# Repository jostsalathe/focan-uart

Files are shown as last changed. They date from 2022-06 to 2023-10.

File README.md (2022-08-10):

# focan-uart

Reverse engineering effort for the UART protocol used between Focan E-Scooter/-Bike displays (GZ3 is the actual test subject) and motor controllers.

## physical interface

The pinout of the connectors can be acquired from the *DU*s [user manual](./doc/2022-06-29%20Focan%20GZ-3%20user%20manual.pdf) and here are some additional details I deduced with the help of a multimeter and an oscilloscope:

| Pin # | Wire color | Function | Driven by | note |
| --- | --- | --- | --- | --- |
| 1 | red | battery voltage | *MCU* | *DU* draws about 11 mA when *MCU* is disconnected and 40 mA during normal operation (without lights). |
| 2 | blue | controller power | *DU* | This supplies power to the *MCU* including lights. *MCU* without lights draws about 29 mA during normal operation. |
| 3 | black | ground | *common* | Swapping this wire with #2 kills the *DU*. Ask me how I know. |
| 4 | green | UART RX | *MCU* to 0~3.32 V |  |
| 5 | yellow | UART TX | *DU* to 0~3.48 V | *MCU* connects 5k6 pullup from 5 V when `controller power` is supplied by *DU* |

## protocol analysis

The protocol analysis and documentation can be found in [./protocolAnalysis/README.md](./protocolAnalysis/README.md).

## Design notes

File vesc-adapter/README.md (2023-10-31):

# Adapter board for using the original Focan GZ3 Display for controlling a VESC6 motor controller

This project uses the UART interface of the VESC6 to translate the commands from the display unit to control and config commands for the VESC6 and extract motor status data from it to report sensible data back to the display unit.

The adapter also has to incorporate power distribution to the vehicle lighting as well as evaluation circuitry and logic for the break lever switches to cut power when breaks are applied (maybe even gradually apply regen?).

## shutting down the ESC

The display unit has a return path for the battery voltage which it switches on when it is turned on. This can be loaded with a few hundred mA. It originally enabled the motor controller and supplied the lights. But motor current would not run through this detour path.

The VESC6 has no enable input so we need a power switch to shut it off when the enable signal from the display unit is off. I started work on implementing a high side switch with a P channel MOSFET (turns out, one wouldn't be enough to dissipate the RDSon losses, two to four would be better).

I then realized by sheer luck through this [blog post](https://civilpedia.org/p/?t=Adding-Shutdown-to-VESC-6&pid=381) that the voltage supply on the VESC6 utilizes the buck converter that is integrated into the DRV8301 MOSFET driver IC to feed all the logic voltages. That IC has an enable pin for that buck converter that is unconnected (pulled high through internal pullup) on the VESC6 board.

When I pull that pin low, the whole VESC6 board only draws 0.74 mA @ 30 V. And the adapter board will also be supplied by this buck converter, so would draw nothing when disabled.

The approach in the aforementioned blog post should be suitable to our application as well. I have some 3V Zener diodes in stock. I measured the pullup current out of the Buck_En pin to be about 1.1 uA so 150k resistors should be plenty small to reliably pull the pin low whilst not wasting energy.

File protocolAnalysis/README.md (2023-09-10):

# High Level Analyzer for Saleae Logic 2

The protocol is analyzed by capturing the communication with a logic analyzer and looking for patterns. Any gained knowledge is then put into high level analyzer plugins (*HLA*) for that logic analyzer. This enables ongoing verification of previous insights.

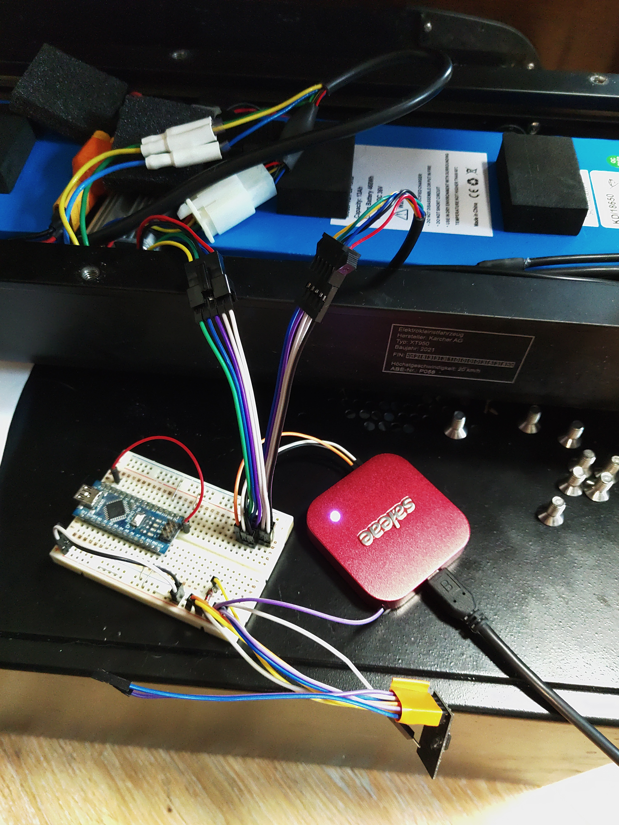
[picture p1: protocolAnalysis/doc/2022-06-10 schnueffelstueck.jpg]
Schnueffelstueck


There is one HLA each for the UART signal between the display unit (*DU*) and the motor control unit (*MCU*):

* `FocanGZ3-TX`: *DU* -> *MCU*
* `FocanGZ3-RX`: *MCU* -> *DU*

## General protocol description

The communication works with full duplex UART at about 3.5 V logic level running at 9600 baud.

As long as the *DU* is turned on, it will send a data frame to the *MCU* via the TX signal roughly every 0.1 seconds. The *MCU* will then reply to that via the RX signal.

## TX data frame

Each TX data frame consists of 20 bytes describing the whole configuration and state of the *DU*.

| **offset** | **mask** | **name** | **description** |
| --- | --- | --- | --- |
| 0x00 | 0xFF | device address (?) | seems to be always 1 in TX direction |
| 0x01 | 0xFF | data frame length | always 20  (0x14) in TX direction |
| 0x02 | 0xFF | protocol revision (?) | seems to be always 1 in both directions |
| *0x03* | *0xFC* | *unknown* |  |
| 0x03 | 0x03 | drive mode | 0: pedal drive, 1: electric drive, 2: both (set with P10) |
| *0x04* | *0xF0* | *unknown* |  |
| 0x04 | 0x0C | gear | 0: off, 1: eco, 2: mid, 3: high |
| 0x04 | 0x03 | gear again | repeated for some reason ¯\\\_(ツ)\_/¯ |
| *0x05* | *0x80* | *unknown* |  |
| 0x05 | 0x40 | kick start | 0: motor can start from still stand, 1: motor must turn before it can start (set with P09) |
| 0x05 | 0x20 | light enable | 0: light off, 1: light on |
| *0x05* | *0x1F* | *unknown* |  |
| 0x06 | 0xFF | number of speed magnets | ranging from 0 to 255 (set with P07) |
| *0x07* | *0xFE* | *unknown* |  |
| 0x07 | 0x01 | wheel diameter high | high byte of the following |
| 0x08 | 0xFF | wheel diameter low | in 1/10 inch ranging from 25 to 500 (set with P06) |
| *0x09* | *0xE0* | *unknown* |  |
| 0x09 | 0x1F | boost sensitivity | ranging from 1 to 24 (set with P11) |
| *0x0A* | *0xF8* | *unknown* |  |
| 0x0A | 0x07 | boost start strength | ranging from 0 to 5 (set with P12) |
| *0x0B* | *0xFF* | *unknown* |  |
| *0x0C* | *0x80* | *unknown* |  |
| 0x0C | 0x7F | speed limit | in km/h ranging from 0 to 100 (set with P08) |
| *0x0D* | *0xE0* | *unknown* |  |
| 0x0D | 0x1F | current limit | in A ranging from 1 to 20 (set with P14) |
| *0x0E* | *0xFC* | *unknown* | (maybe belonging to the following) |
| 0x0E | 0x03 | undervolt threshold high | high byte of the following |
| 0x0F | 0xFF | undervolt threshold low | in 1/10 volt (combination of P03 (range: 24V/36V/48V) and P15 (decivolt adjustment) |
| *0x10* | *0xFC* | *unknown* |  |
| 0x10 | 0x03 | speed lever position high | high byte of the following |
| 0x11 | 0xFF | speed lever position low | ranging from 0 to 1000 |
| *0x12* | *0x80* | *unknown* |  |
| 0x12 | 0x40 | cruise enable | (set with P17) |
| *0x12* | *0x30* | *unknown* |  |
| 0x12 | 0x0F | power magnetic steel disc type | 5/8/12 (set with P13) |
| 0x13 | 0xFF | CRC | check sum |

The CRC sum is calculated with the following algorithm parameters determined by the program [reveng](https://reveng.sourceforge.io/readme.htm) using captured samples:

`width=8  poly=0x01  init=0x00  refin=false  refout=false  xorout=0x00  check=0x31  residue=0x00  name=(none)`

## RX data frame

Each RX data frame consists of 14 bytes describing the state of the *MCU*.

| offset | mask | name | description |
| --- | --- | --- | --- |
| 0x00 | 0xFF | device address (?) | seems to be always 2 in RX direction |
| 0x01 | 0xFF | data frame length | always 14 (0x0E) in RX direction |
| 0x02 | 0xFF | protocol revision (?) | seems to be always 1 in both directions |
| *0x03* | *0xFF* | *unknown* |  |
| *0x04* | *0xFF* | *unknown* |  |
| *0x05* | *0xFF* | *unknown* |  |
| *0x06* | *0xFF* | *unknown* |  |
| *0x07* | *0xFF* | *unknown* |  |
| *0x08* | *0x80* | *unknown* |  |
| 0x08 | 0x7F | wheel speed high | high byte of the following |
| 0x09 | 0xFF | wheel speed low | in milliseconds/revolution ranging from 0 to 31456 |
| *0x0A* | *0xFF* | *unknown* |  |
| *0x0B* | *0xFF* | *unknown* |  |
| *0x0C* | *0xFF* | *unknown* |  |
| 0x0D | 0xFF | CRC | check sum |

The vehicle velocity `v[km/h]` can be calculated from the wheel speed `t[ms]` using the known wheel diameter `D[in]` like this:

```
circumference C[m] = 0.0254 m/in * D * PI

v = 1000 ms/s * 3600 s/h * 0.001 km/m * C / t
v = 3600 * C / t
v = 3600 * 0.0254 * D * PI / t
v = 91.44 * PI * D / t
```

The CRC sum uses the same algorithm as TX direction.

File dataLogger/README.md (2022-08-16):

# Data Logger

This is a small PCB for logging and manipulating the communication between the display and the motor controller.

## Features

* microSD card slot
  * saving logs (one file per power cycle / ride)
  * configuration file
* 2 * JST SM 5 pin connections one male and one female for communication to/from display and motor controller
* Microcontroller ESP32
  * WiFi for configuration, internet time and accessing log files
  * SPI for SD card
  * 2 spare UARTs for communication to/from display and motor controller
  * RTC for accurate time stamps in file name and log entries

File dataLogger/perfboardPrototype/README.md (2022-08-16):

# Perfboard Prototype

## Used Parts

* ESP32-WROOM-32D module (U2)
* SPI MicroSD card module (J_SD1)
* DM01 V2.0 fixed voltabe buck converter module (52 V max input, 3.3 V out) (U1)
* 70 mm * 30 mm perforated prototyping board
* 470k 1% axial 1/4 W resistor (R2), 12k 1% 0603 1/10W SMD resistor (R3) and 100nF 0603 SMD capacitor (C1) for measuring battery voltage
* 10k 1% axial 1/4 W resistor (R4) and some 3V zener diode (D1) for wakeup pin
* 10k 1% axial 1/4 W resistor for EN pin pullup (R1)
* JST-SM 5 pin connectors, one of each gender (J_DU1 and J_MCU1)
* 5 pin socket for flashing firmware and debugging (J_PRG1)

## Pinout

| connector | pin# | signal name | ESP32 pin | description |
| --- | --- | --- | --- | --- |
| J_PRG1 | 1 | GND | GND | ground connection of programmer |
| J_PRG1 | 2 | TX_DBG | IO1 | UART TX to programmer |
| J_PRG1 | 3 | RX_DBG | IO3 | UART RX from programmer |
| J_PRG1 | 4 | BOOT | IO0 | boot mode with internal pullup |
| J_PRG1 | 5 | EN | EN | enable with external pullup (R1) |
| J_DU1/J_MCU1 | 1 | +BATT | IO39 | battery voltage that supplies this unit |
| J_DU1/J_MCU1 | 2 | PWR_MCU | IO34 | The DU feeds battery power to the MCU via this connection when it is on. Use this signal to wake from deep sleep. |
| J_DU1/J_MCU1 | 3 | GND | GND | ground connection for external hardware |
| J_DU1 | 4 | TX1 | IO17 | UART TX to DU |
| J_DU1 | 5 | RX1 | IO16 | UART RX from DU |
| J_MCU1 | 4 | RX2 | IO19 | UART RX from MCU |
| J_MCU1 | 5 | TX2 | IO18 | UART TX to MCU |
| J_SD1 | 1 | 3V3 | VDD | supply voltage for MicroSD card |
| J_SD1 | 2 | CS | IO32 | chip select for MicroSD card |
| J_SD1 | 3 | MOSI | IO33 | serial data to MicroSD card |
| J_SD1 | 4 | CLK | IO26 | serial clock for MicroSD card |
| J_SD1 | 5 | MISO | IO14 | serial data from MicroSD card |
| J_SD1 | 6 | GND | GND | ground conneciton for MicroSD card |

### Notes on Measuring +BATT

Due to the chosen voltage devider you should call `analogSetAttenuation(ADC_2_5db);`.

With this attenuation setting you should use `double vBat = (analogRead(39) + 272.5) / 77.95;` to calculate the actual battery voltage.

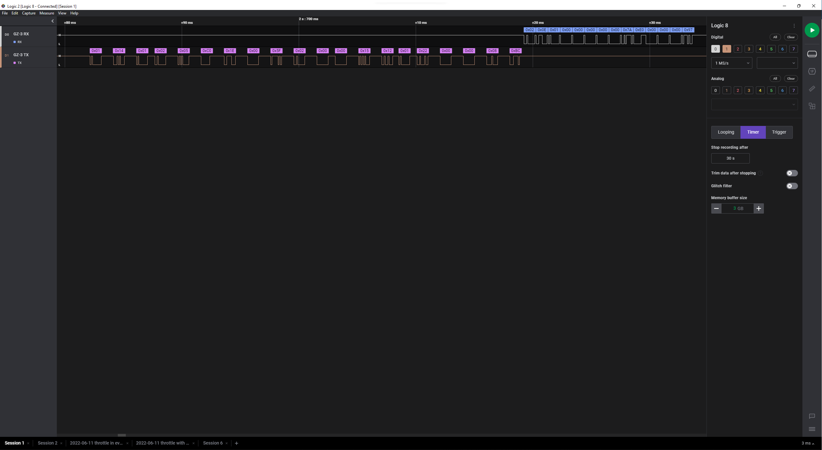
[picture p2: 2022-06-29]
protocolAnalysis/doc/2022-06-11 firstDecodedDatagrams.png

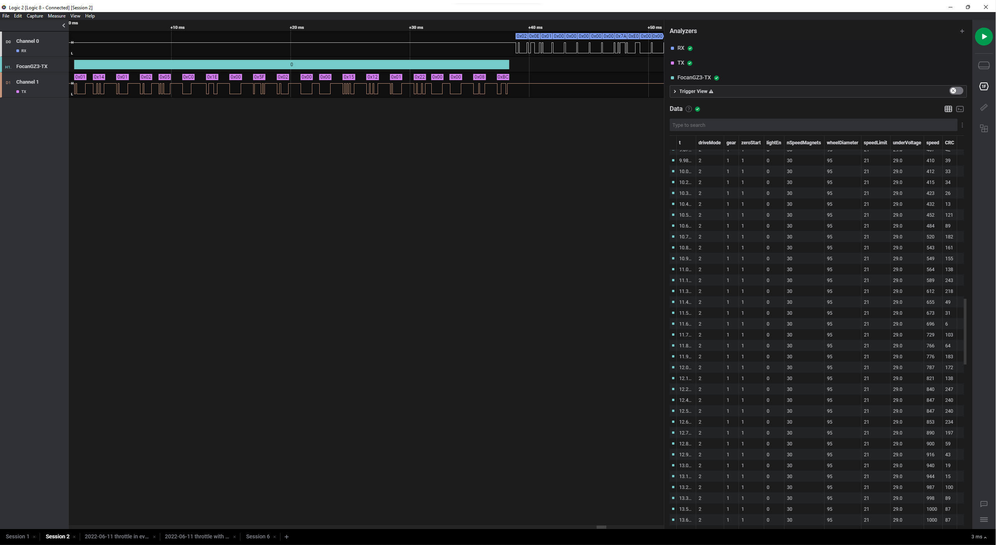
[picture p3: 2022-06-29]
protocolAnalysis/doc/2022-06-11 progressOnDissector.png

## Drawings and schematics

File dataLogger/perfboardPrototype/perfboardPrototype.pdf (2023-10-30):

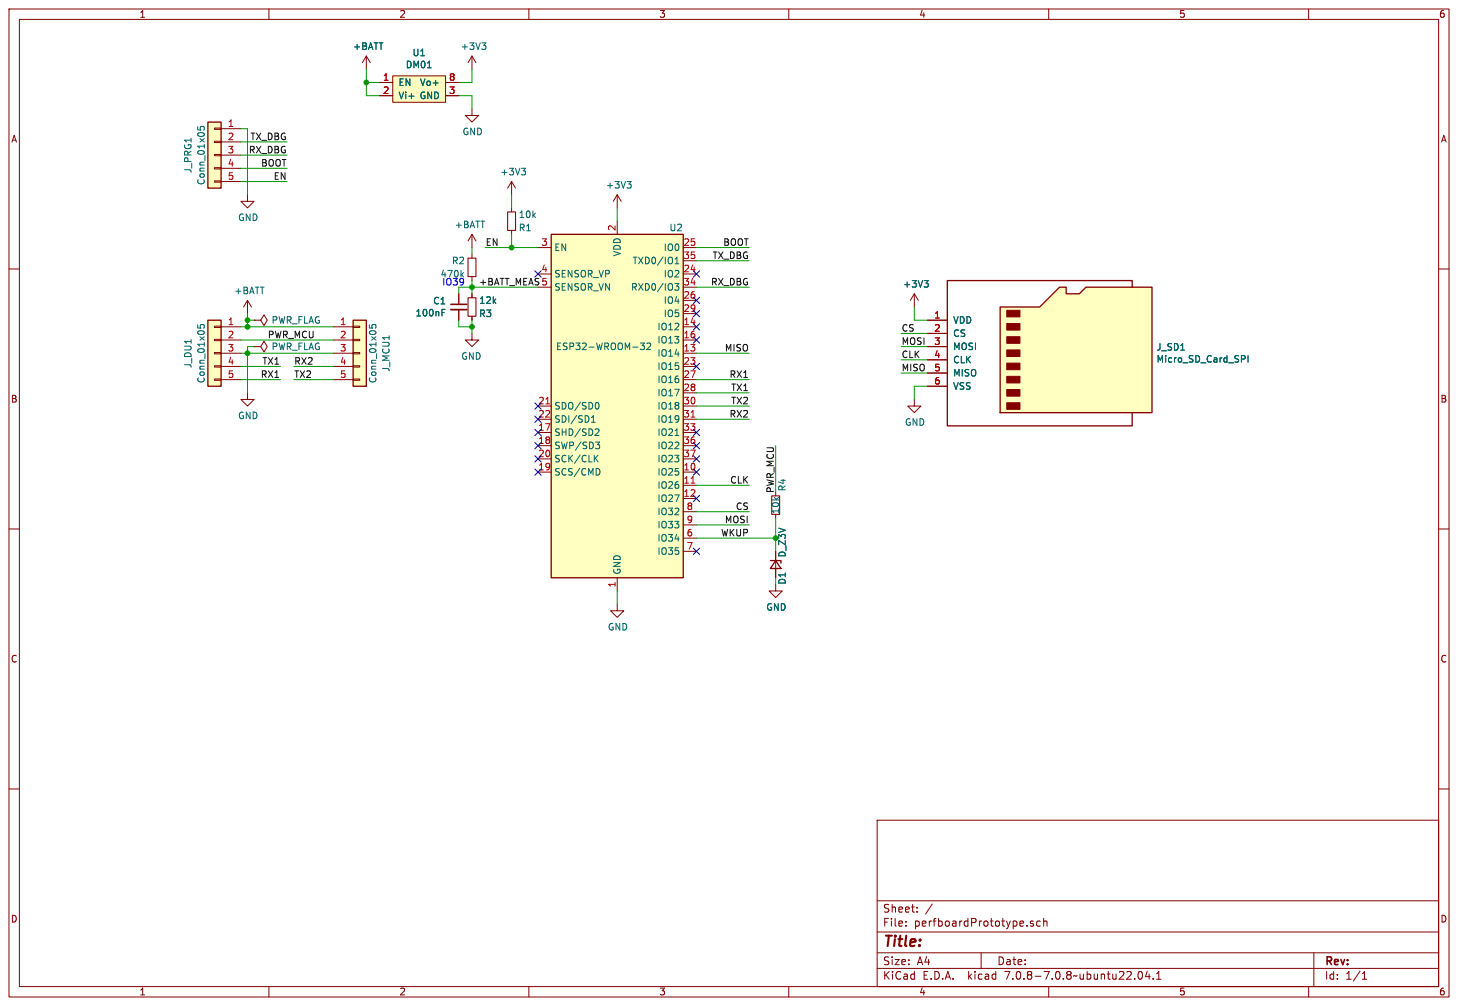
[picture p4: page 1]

2 SCK/CLK 20 SDO/SD0 21 SDI/SD1 22

Id: 1/1 Title: File: perfboardPrototype.sch Sheet: /

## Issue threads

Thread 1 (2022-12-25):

Undervolt Threshold

BastelPichi, 2022-12-25:
Hey,
First of, great work. I've sniffed the communication between an g51 display and controller, and the protocol seems to be the same. Only the undervolt protection is troubling me.

I've recorded the traffic once with 36v, once with 24v. The values I'm getting are 0xD2 and 0x36.
0xD2 makes sence, 0xD2 = 210; 210 * 0.1 = 21V; 21V / 7 = 3V per cell.
However with 36V, it doesn't make any sence at all.
0x36 = 54??? Only sence here would be 0x + appending 36V???

Also, P15 is weird. All manuals say "Unspecified" and I can't set it all on my display...

Do you have any idea on this?

BastelPichi, 2022-12-25:
For 48v, we have 0x9A = 154. Not any sence either.

BastelPichi, 2022-12-25:
Never mind. i can set P15 - Its low voltage cuttoff, 31 for 36V Batterys.

jostsalathe, 2022-12-25:
Hi there, thanks for the feedback!

I have an idea what may be happening on your side: I suspect you only observed the 16th byte (offset 0x0F). This is only the low byte of the `under volt threshold` value. For 24 V batteries, the 210 decivolts fit into one byte so there your reading makes sense. 310 would be 0x136 encoded in hex. You can see the 0x36 you found in your record. I suspect that the byte before that, 15th byte (offset 0x0E), contains 0x00 in your recording with P03 set to 24 V and 0x01 for the 36 V and 48 V settings. This would complete the under volt threshold value.

I hope this reflects your recordings and that I could help you a little with that.

BastelPichi, 2022-12-25:
Thanks! This could be, but im not sure how this could have happened. Maybe I messed up some settings in logic 2... Imma retry with anUSB to UART, to minimize errors. However, from now this should be pretty much straight forward.

Thanks alot and merry christmas!

Closed 2022-12-25.

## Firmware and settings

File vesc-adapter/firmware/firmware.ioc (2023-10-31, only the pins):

Mcu.UserName=STM32F042F6Px
PA0.GPIO_Label=Sw_Breaks
PA0.Signal=GPIO_Input
PA1.GPIO_Label=Light_En
PA1.Signal=GPIO_Output
PA10.GPIO_Label=Display_TX
PA10.Signal=USART1_RX
PA13.Signal=SYS_SWDIO
PA14.Signal=SYS_SWCLK
PA2.GPIO_Label=ESC_RX
PA2.Signal=USART2_TX
PA3.GPIO_Label=ESC_TX
PA3.Signal=USART2_RX
PA4.GPIO_Label=Sw_Blink_Right
PA4.Signal=GPIO_Input
PA5.GPIO_Label=Sw_Blink_Left
PA5.Signal=GPIO_Input
PA6.GPIO_Label=Blinker_Right_En
PA6.Signal=S_TIM3_CH1
PA7.GPIO_Label=Blinker_Left_En
PA7.Signal=S_TIM3_CH2
PA9.GPIO_Label=Display_RX
PA9.Signal=USART1_TX
PB1.GPIO_Label=U_Bat_Sense
PB1.Signal=ADC_IN9
PB8.GPIO_Label=Sw_Boot
PB8.Signal=GPIO_Input
PF0-OSC_IN.Signal=RCC_OSC_IN
PF1-OSC_OUT.GPIO_Label=Led_Debug
PF1-OSC_OUT.Signal=GPIO_Output

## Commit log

2022-06-29 HLAs are usable but not complete. README files reflect my current knowledge of this protocol. Started gathering suitable components for a data logger module to inject between the display and the moto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
    [2022-06-10 on-0-100-0-off.ods, 2022-06-12 originalDisplay.csv]
2022-08-11 Completed schematics for perfboard prototype. Tried some visualization and layout planning in Pcbnew with mixed results.
    [perfboardPrototype.kicad_pcb, perfboardPrototype.sch]
2022-08-14 Removed Zeners from UART pins because the voltage there coming from external components should be okay for the ESP32. Shifted some pins around for better layout on perfboard.
    [perfboardPrototype.sch]
2022-08-16 Updated some documentation of perfboard prototype.
    [perfboardPrototype.sch]
2023-10-30 started work on adapter module between original display unit and a VESC
    [hardware.kicad_pcb, hardware.kicad_sch]
2023-10-30 updated perfboardPrototype to KiCad 7 format and added schematics pdf
    [perfboardPrototype.kicad_pcb, perfboardPrototype.kicad_sch, perfboardPrototype.sch]
2023-10-31 added zener diode option parallel to R1, added pull-down-R to Q2, added debouncing circuits to external switches, removed internal pull-Rs from MCU configuration
    [hardware.kicad_sch]
2023-10-31 moved vesc-adapter stuff to a more sensible location
    [hardware.kicad_pcb, hardware.kicad_sch]
2023-10-31 added solder pads for battery connections, added footprints to everything
    [hardware.kicad_sch]
2023-10-31 added notes about VESC6 power off options (maybe use DRV8301 Buck_EN pin?)
